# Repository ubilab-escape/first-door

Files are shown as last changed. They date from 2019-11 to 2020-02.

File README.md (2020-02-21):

# Group 4:  First door #
Our group works on the automated doors in the escape room as well on the puzzle for the first door.

## Content
* [Part in the Escape Room](#1)
* [Project Timeline](#2)
* [Using the code](#7)
* [First Puzzle](#4)
* [Doors](#5)
* [Plasma Globes](#6)

## Part in the Escape Room 
After the mission briefing the participants will enter the anterior room.
In the story this will be the room of the security even though the security will be absent for the whole game.

The participants have to solve a first puzzle to open the first door and to be able to move to the second, adjencted room which will be the computer lab room. After all players are situated in the second room, the first door should close.

There the players again have to solve various riddles and puzzle to get into the server room. The door between lab and serverroom will be implemented by us.

## Project Timeline 
- [x] Concept finding for door mechanism, puzzles and dead man switches
- [x] Composition of a part list
- [x] Installing of the doors
- [x] Software development of the doors and electrical installation
- [x] Software development of the riddle and installation of its needed components
- [x] Software development of the MQTT communication
- [x] Testing of the door and riddle components over MQTT
- [x] Testing of the voltage/current course of the plasma globes
- [x] Software implementation of the plasma globes
- [x] 3D printing of fixations and riddle housing
- [x] Testing of the interaction of all components
- [x] Implementation and control over the LED stripes from the Environment Group
- [x] Last testing and bug fixing
- [x] Final run and presentation

## Using the Code 
### General
* WiFi- credentials are not included in the code. Before uploading via OTA, ensure that the correct WiFi credentials are set in the code!

### Door Code
* Ensure that the #define macro DOOR1 or DOOR2 is set according to which door you want to use the code for

### Plasma Globes
* When you change the mdns name via MQTT, this will also change the ID of the globe (gets written to EEPROM). Use the Format "GlobeX" as new name, e.g. "Globe0" for the Master Globe.
* Max. 4 globes can be used (IDs: 0,1,2,3)

### MQTT interaction
* The commands for controlling the implemented stages can be found in the document linked at the end of this readme!

## First Puzzle 
### Stage ###
After the mission briefing, the participants are in the anteroom and need to get access to the labroom.

### Concept and Idea ###
Story: The absent security man likes to listen to music on his MP3-Player while at work. This MP3 contains several songs as well as an **audio morse code**. Using the help of a hidden morse alphabet in the room the players will be able to solve the puzzle and obtain a code.
Morse alphabet test

The obtained code has to be inserted into a keypad with an LCD display.

### Hardware ###
* MP3 Player
* 3D printed Input interface consisting of 
	* LCD display
	* 4x4 matrix keypad
	* ESP32

The parts for 3D printing the input interface can be founded [here](https://github.com/ubilab-escape/first-door/tree/master/3D%20Printing)
### Software ###
[Code](https://github.com/ubilab-escape/first-door/tree/master/Final%20Code/First_Puzzle_final)

The following flow chart only represents the basic function of the code and does not show every detail!

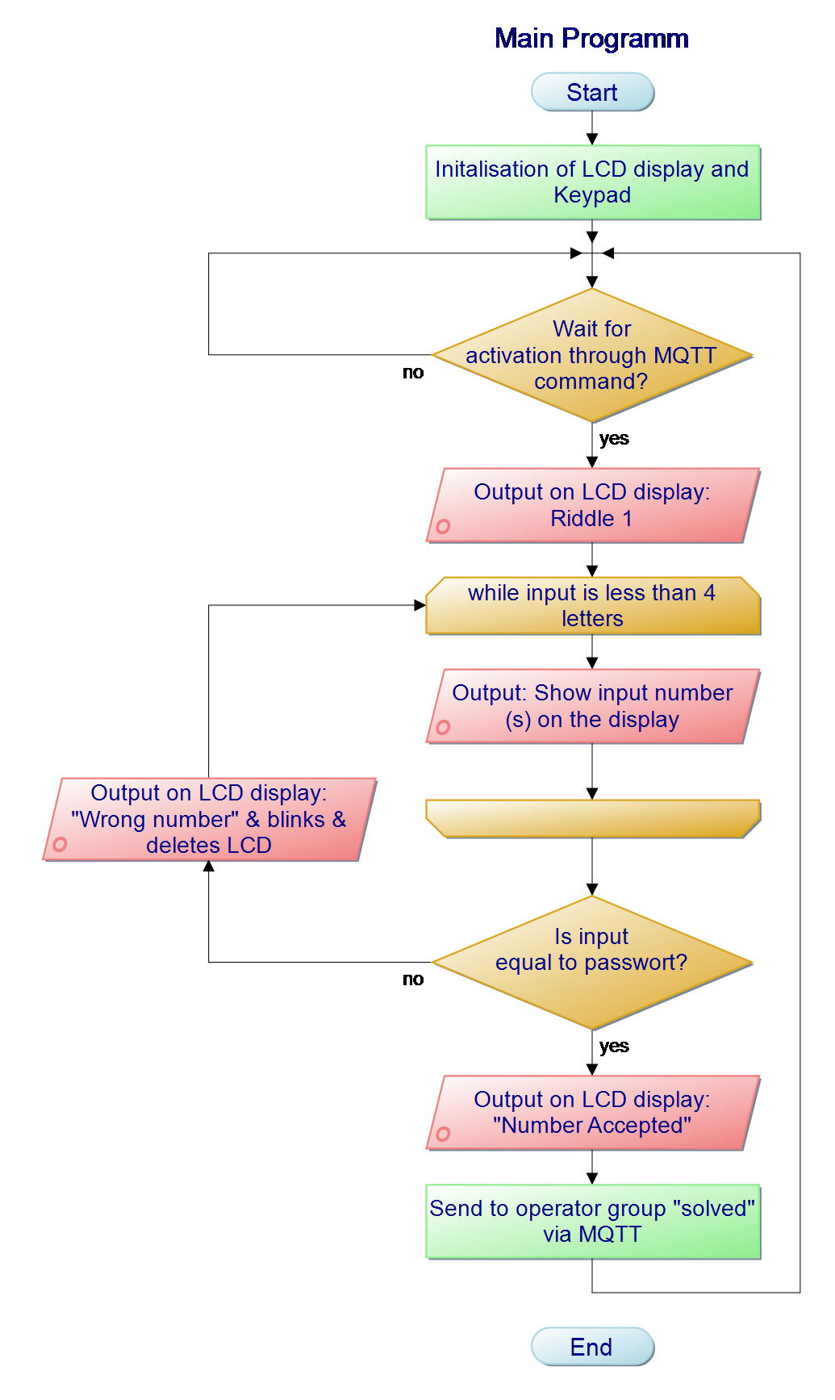
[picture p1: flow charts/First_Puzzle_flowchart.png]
flow chart puzzle 1


## Doors 
### Stage ###
Door 1:
This is the door between anteroom and labroom. This door should open after solving the first puzzle (Morse Code Puzzle) and close after all participants entered the labroom. After the participants were able to solve all other riddles the door should open again to let the players escape.

Door 2:
This door seperates the labroom from the serverroom. After solving all puzzles in the labroom this door will open automatically and provide access to the serverroom.

### Concept and Idea ###
* both doors should open automatically and have to be controllable by the operator via MQTT commands
* a detection mechanism should be implemented for localization of participants standing in between the door frame while closing
* the participants shouldn't be able to open the doors manually by hand (--> lock)

A concept of a sliding door with a toothbelt mechanism was developed. The door is suspended and guided through a linear sliding rail on the upper door frame. Furthermore a U-profile duct was mounted for guidance at the bottom. The door movement is achieved by a toothbelt mechanism. Both ends of the toothbelt are fixed on the door. Return shafts on both sides of the door frame are redirecting the toothbelt. Also one return shaft is connected to the stepper motor axes. Mechanical switches (endstops) on both sides detect either closed or opened position.

An obstacle detection in the closing area could be avoided through the usage of the Plasma Globes. Every participant in the Escape Room has to touch one Plasma Globe for closing the door. A person in the closing area is therefore impossible. Also, the toothbelt slides over the return shaft, as soon as the door faces a slight resistance.

Not implemented / possible improvements:
* electrical door lock: solved by leaving driving stage "on" while door is closed, so that more force is needed to push it open.

### Hardware ###
* ESP32
* stepper motor + appropriate driver
* 24V power supply
* buck converter for ESP32 power supply (24V --> 5V)
* tooth belt
* toothbelt disk
* end stop switches
* linear rail
* sliding suspension bracket
* door material (wooden plates)
* U-profile duct

### Software
[Door - Code](https://github.com/ubilab-escape/first-door/tree/master/Final%20Code/Door)

In the following the velocity profile of the door is shown. 

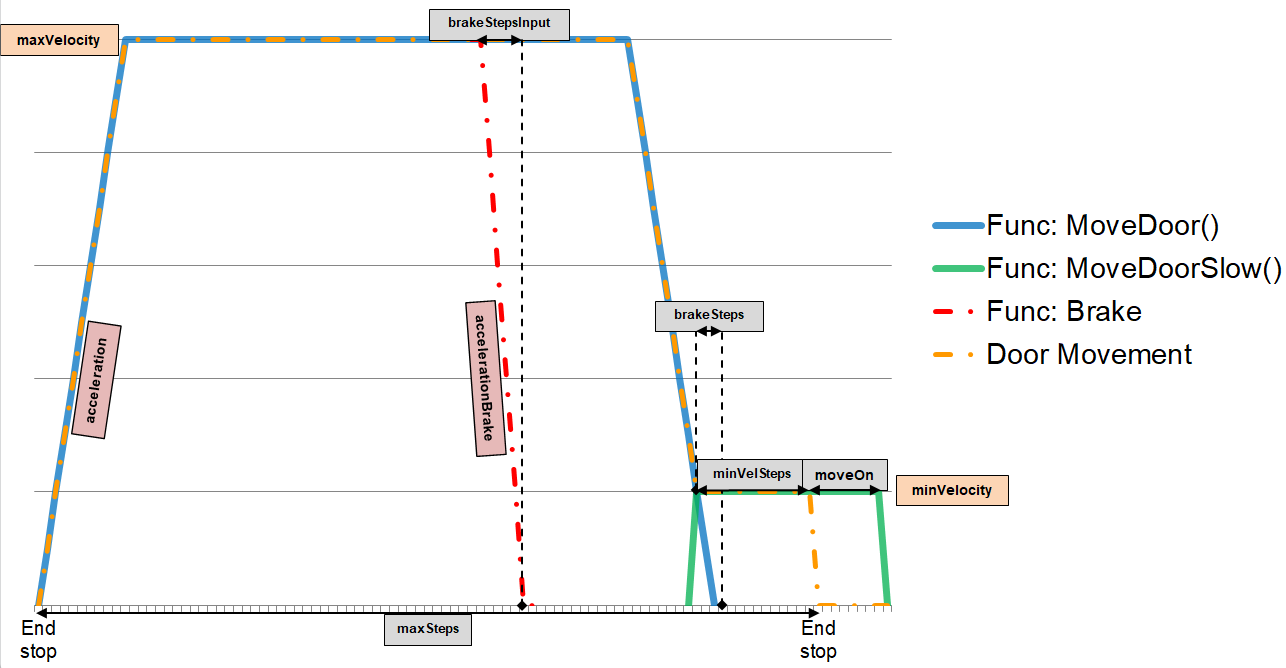
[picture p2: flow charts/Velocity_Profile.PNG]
Velocity_profile


* Acceleration, velocity and distance parameters (acceleration / accelerationBrake / maxVelocity / minVelocity / minVelSteps / moveOn) must be chosen before code flashing.
* The parameters brakeSteps and brakeStepsInput are calculated by 0.5*minvelocity^2/acceleration or 0.5*maxVelocitty^2/accelerationBrake. 
* The parameter maxSteps is set and the variable curPos is reset after calibration.

The programming flowchart is attached in the following. The flow chart only represents the basic function of the code and does not show every detail!

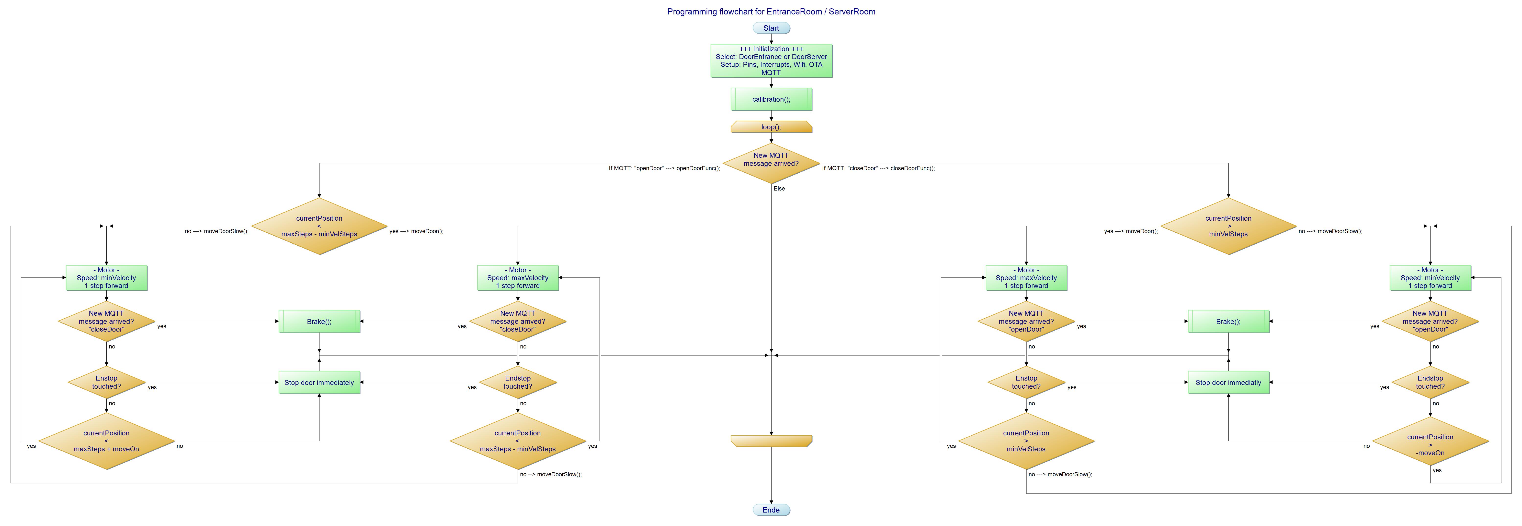
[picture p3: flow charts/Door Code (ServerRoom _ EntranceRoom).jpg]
FlowChart_door


## Plasma globes 
### Stage ###
When the first door opens, participants enter the labroom. There, all lights are off and the plasma globes are activated. The participants must touch all plasma balls simultaneously so that the first door can close and the game continues.

### Concept and Idea ###
* plasma globes draw significantly more current when touched so they can be used as switch
* 4 plasma globes spread across the room at the walls (not possible to touch more than one globe simultaneously)
* Each plasma globe is a standalone unit with own "PowerMeter"
* One "master" device, the other globes are slaves
* operator sends #participants, then each globe determines if it is activated or deactivated (according to globe ID which can be set over MQTT)
* Slave globes:
	* check if globe is touched
	* send touched/ untouched message to master globe
* Master globes:
	* check if globe is touched
	* count number of touched slaves
	* trigger opening of door if all participating globes are touched simultaneously
	* trigger closing of door if not all participating globes are touched
	* activate environment LEDs according to number of touched slaves to provide feedback to the user
	* deactivates all globes as soon as door is closed and send puzzle solved message

### Hardware ###
* PowerMeter (hardware box containing ESP8266 and AC current/voltage sensor )
* 4 usb powered plasma globes

The files for the 3D printed mounting can be found [here](https://github.com/ubilab-escape/first-door/tree/master/3D%20Printing)

### Software ###
[Master Globe - Code](https://github.com/ubilab-escape/first-door/tree/master/Final%20Code/PowerMeter_plasma_master)

[Slave Globe - Code](https://github.com/ubilab-escape/first-door/tree/master/Final%20Code/PowerMeter_plasma_slaves)

The following flow chart only represents the basic function of the code and does not show every detail!
This flow chart represents the master instance, slaves work similar, but without logic for door interaction.
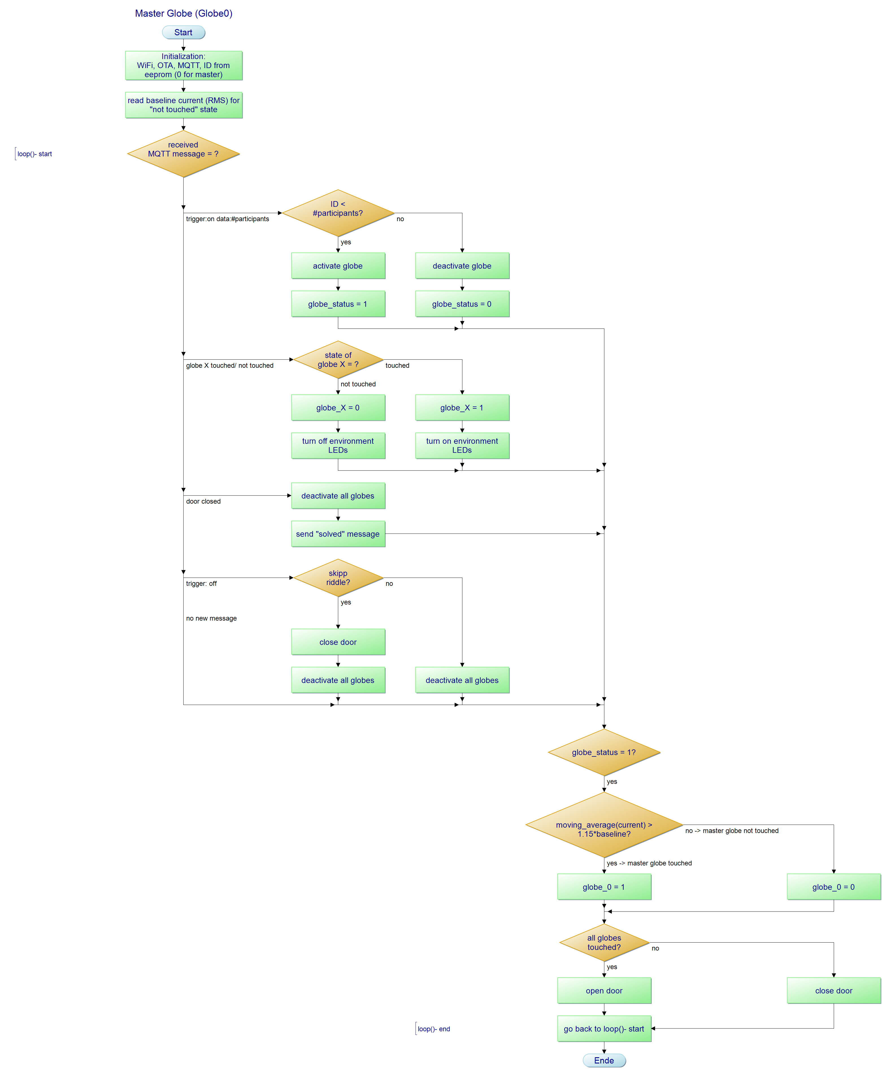
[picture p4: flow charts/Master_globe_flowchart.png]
flow chart puzzle 1


## MQTT Communication ##
The MQTT communication that was initially developed with the operator group can be found here (not every detail was implemented):
* [Doors](https://github.com/ubilab-escape/operator/blob/master/doc/design/group_4_door.svg "Doors")
* [First Puzzle](https://github.com/ubilab-escape/operator/blob/master/doc/design/group_4_puzzle_entrance_door.svg "First Puzzle")
* [Plasma Globe Puzzle](https://github.com/ubilab-escape/operator/blob/master/doc/design/group_4_puzzle_globes.svg "Plasma Globe Puzzle")

For controlling the described escape room parts of our group, use the commands in the following document:
[MQTT commands](https://github.com/ubilab-escape/first-door/blob/master/MQTT_publish_messages.docx "MQTT commands")

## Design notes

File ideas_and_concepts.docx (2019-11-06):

Ideas of Group #4: Both doors & first puzzle

Puzzle:

A wooden cylinder is physically given with a cord which is wound exactly four times around the cylinder. Thereby one end of the cord must touch one end of the cylinder so that the cord extends over the entire cylinder (see figure).

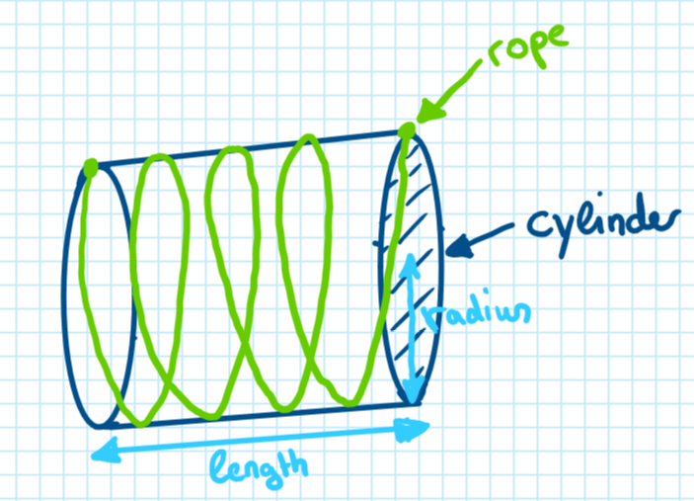
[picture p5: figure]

The task is to calculate the length of the cord. Given parameters are the radius and the length of the cylinder.

The result must then be entered into a keypad (binary or decimal system). If the result is correct the first door will open and the participants will get access for the lab room.

Doors:

- Doors

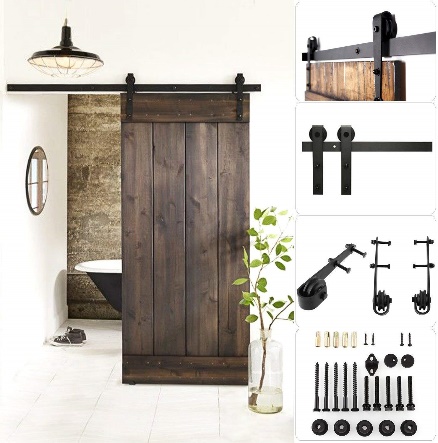
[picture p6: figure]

- Material: Wooden door, either old door which we cut in size or wood board
- Mounting: Sliding door mounting e.g.
- Other required hardware:
  - Screws and nails
  - Percussion drill
  - Drill machine
- Mechanism
  - Alternative A: Pull rope mechanics

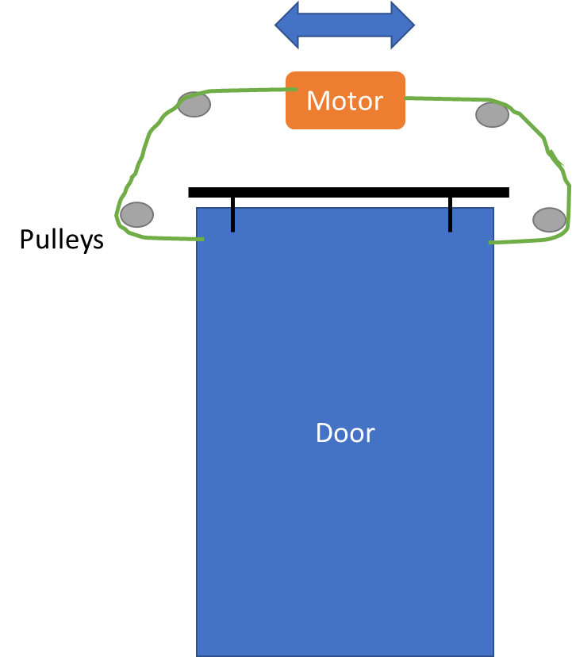
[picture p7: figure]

Required hardware: Pulleys, gearwheels, rope, mounting devices

  - Alternative B: Gear mechanics

3) Detection of objects in closing area

Concept: Use infrared emitter and sensors to detect if the door area is free in order to close the door.

Also use a pressure sensor to feedback that the door is closed

4) Detection of participants in Lab Room:

- Concept A: Dead-man-switches spread across lab room have to be activated → 1st door closes and adventure continues
- Hardware: Plasma globe / simple switch, current sensor (shunt resistor), uC/ relais, wiring
- Current flow through plasma globe changes when touched by hands → measure current flow with shunt resistor and close door when each plasma globe is touched (make sure by positioning that no person can reach more than one plasma globe simultaneously)
- Remark: Reliability of “plasma globe switch” has to be tested and in worst case exchanged by simple button switches
- Concept B: Using Group 9 locating the group members

Other required hardware

- Microcontroller with WLAN function / shield

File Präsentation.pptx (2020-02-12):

## Project „Escape Room“

Group 4 – Doors and first puzzle
David, Mario, Sarah

## Interactions

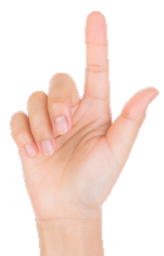
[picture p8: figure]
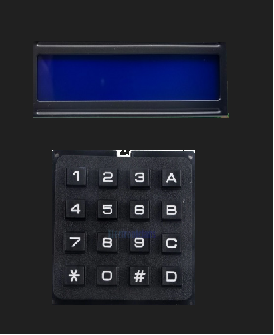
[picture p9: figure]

RIGHT

open

## Interactions

close

## How does this communciation work? -> MQTT

Puzzle

Activated/inactivated

open/close

Door 1

solved

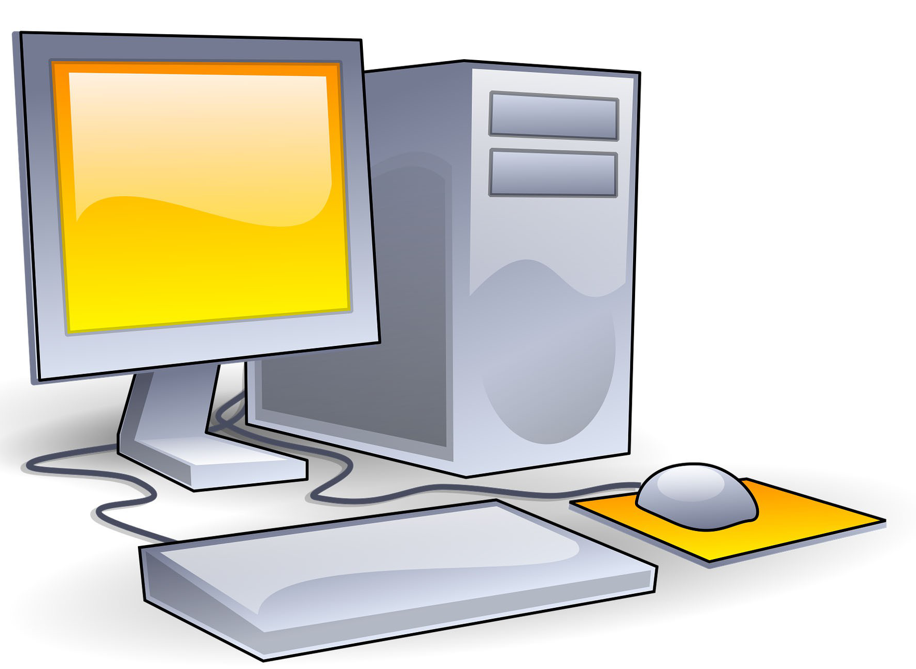
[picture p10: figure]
Bildergebnis für computer

Server

open/close

Door 2

open/close

Activated/
inactivated

Touched/
not touched

Globes

## Puzzle

Components:
- 16x2 IC2 LCD Display
- 4x4 Matrix Keypad
- 3D printed housing
Microcontroller:
- ESP32
Communication between microcontroller and components:
- I2C Interface to LCD display
- Analog Inputs to Keypad

## Puzzle

no

Right password entered?

Initialisation

yes

Send via MQTT: Puzzle solved -> Door will open

## Doors

Mechanical components:
- Mounting
- Gearbelts
- Gearwheels
- Floor guide rail
- Endstops
Electrical compnents:
- Motor and Driver
- Endstops switches
- Voltage supply
Microcontroller:
- ESP 32

## Doors

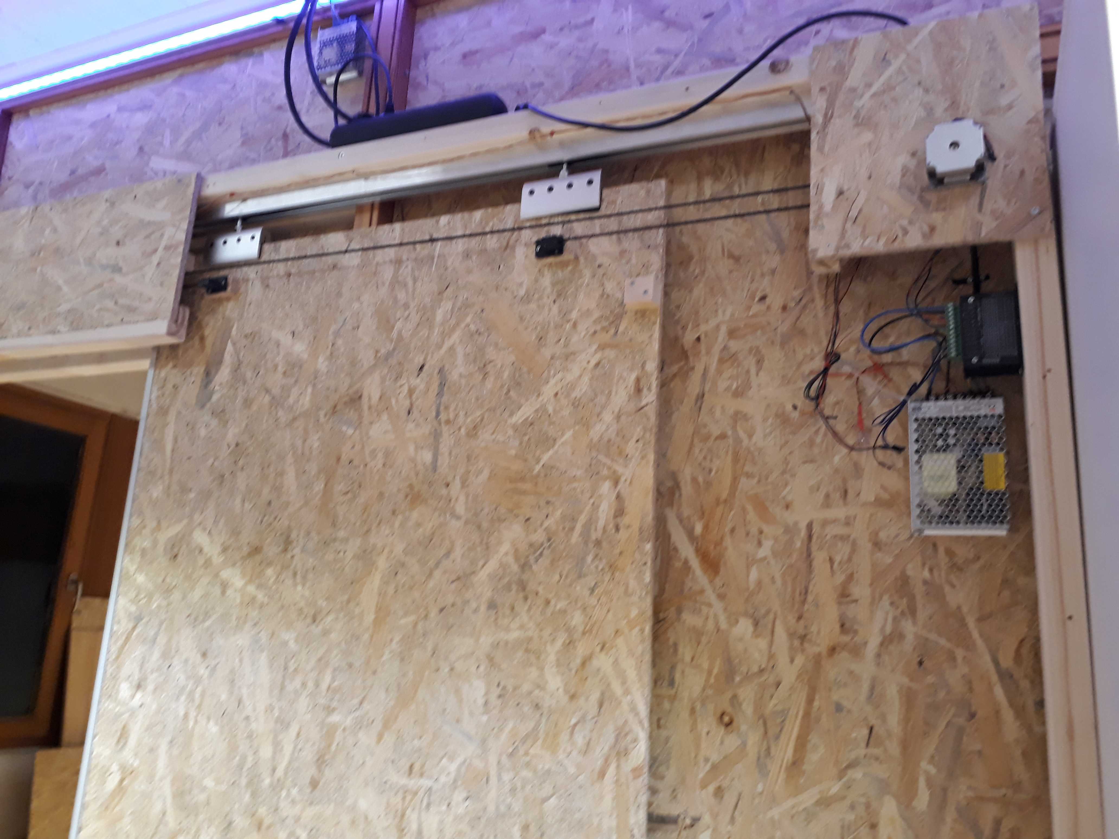
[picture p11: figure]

Mechanical components:
- Mounting
- Gearbelts
- Gearwheels
- Floor guide rail
- Endstops
Electrical compnents:
- Motor and Driver
- Endstops switches
- Voltage supply
Microcontroller:
- ESP 32

## Doors – Functional principle

Initialisation

Slowly move door in one direction

Endstop
touched?

yes

Repeat some for other side

Save Endpositions

no

Move the door to the respective end stop

Move the door to the respective end stop

Get command: „open“

Send MQTT message: open

Send MQTT message: closed

Get command: „close“

## Plasma Globes – Sensing touch events

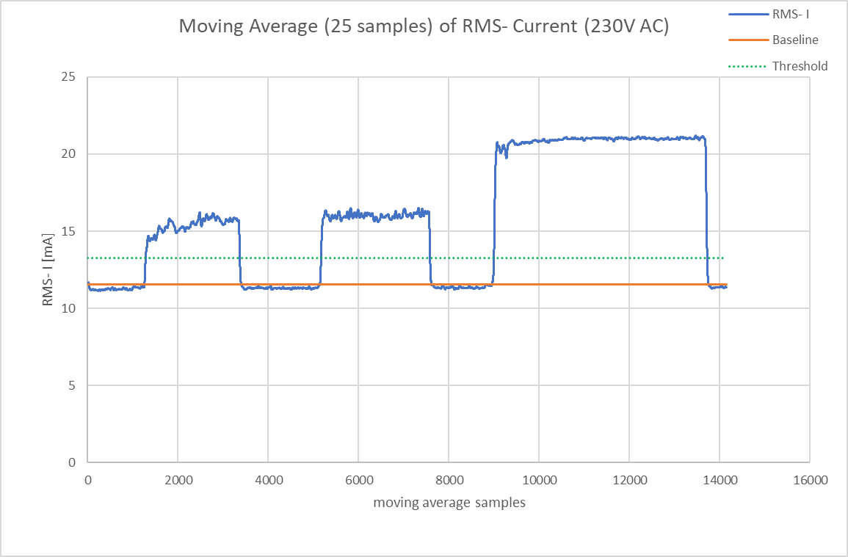
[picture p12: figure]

touched

touched

touched

## Plasma Globes - Puzzle

open/close

touched/ not touched

closed!

close

open

master

touched/ not touched

slave

touched/ not touched

slave

slave

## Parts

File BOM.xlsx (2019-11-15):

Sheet: Finale_BOM
BOM | Teil | Eigenschaften | Kosten | Stück |  | Link
Tür
Mechanik oben: Set |  |  | 34.65 | 2 | 69.3 | https://www.amazon.de/GEZE-Rollan-Schiebet%C3%BCrbeschlag-Schiebet%C3%BCr-T%C3%BCrbreite/dp/B000VD8YI6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
Führungsschiene unten |  | U- Profil |  |  | 0 | Baumarkt
Rahmen |  |  |  |  | 0
Konstruktionsvollholz |  |  | 35 € | 1 | 35 | https://www.obi.de/bauholz/konstruktionsvollholz-brettschichtholz/c/1823
Schrauben |  |  |  |  | 0
Tür |  |  |  |  | 0
Sperrholz Pappel |  |  | 18 € | 2 | 36 | https://www.bauhaus.info/zuschnittplatten/sperrholzplatte-nach-mass/p/24815310
 |  |  |  |  | 0
Antrieb |  |  |  |  | 0
Zahnriemen GT2 (M) 10mm |  |  | 9 |  | 0 | https://www.amazon.de/ASHATA-Zahnriemen-3D-Drucker-Riemenscheibe-Synchronriemen-3-Meter/dp/B07PFD7H78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
Zahnriehmenklemmen |  |  |  |  | 0 | Amazon
Zahnriehmenscheiben |  |  |  |  | 0 | Amazon
 |  |  |  |  | 0
Türsicherheit |  |  |  |  | 0
Lichtquelle |  |  | 5 | 1 | 5 | https://www.amazon.de/AZDelivery-%E2%AD%90%E2%AD%90%E2%AD%90%E2%AD%90%E2%AD%90-KY-008-Sensor-Arduino/dp/B07CNGFS8M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
Lichtsensor |  |  | 6 | 1 | 6 | https://www.amazon.de/AZDelivery-Widerstand-Photoresistor-LDR5528-Arduino/dp/B07DDN5TH2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
 |  |  |  |  | 0
Türschloss |  |  |  |  | 0
elektromagn. Riegel |  |  | 16 | 1 | 16 | https://www.amazon.de/ATOPLEE-T%C3%BCr-Fach-Zunge-Down-Elektroschloss-Montag-Magnet-554239mm/dp/B01N650528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
elektromagn. Riegel |  |  | 9 | 2 | 18 | https://www.amazon.de/BQLZR-Schrankt%C2%A8%C2%B9r-Elektroschloss-Montage-Solenoid/dp/B00NE0GHDW
Relais |  |  | 6.19 | 1 | 6.19 | https://www.amazon.de/AZDelivery-1-Relais-KY-019-High-Level-Trigger-Arduino/dp/B07CNR7K9B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
Keypad |  |  | 6 | 1 | 6 | https://www.amazon.de/AZDelivery-4x4-Matrix-Keypad-Tastatur/dp/B07D2FGQL4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
Display |  |  | 5 | 1 | 5 | https://www.amazon.de/dp/B07CQG6CMT
Buck Converter | DC/DC- Wandler | 24V(Netzteil) --> 12V (Riegel) | 3 | 1 | 3 | https://www.conrad.de/de/p/mini-dc-dc-step-down-spannungsregler-mp1584en-buck-power-module-outout-0-8-20v-3a-802244075.html
 |  |  |  |  | 0
Motor- Antrieb |  |  |  |  | 0
Netzteil |  |  |  |  | 0
 | MW LRS-150F-24 Schaltnetzteil | 150 W, 24 V, 6,5 A | 21.65 | 1 | 21.65 | https://www.reichelt.de/schaltnetzteil-geschlossen-150-w-24-v-6-5-a-mw-lrs-150f-24-p202982.html?trstct=pos_6
Kaltgerätestecker |  |  |  |  | 0
 |  |  |  |  | 0
Stromsensorik |  |  |  |  | 0
Motor | INA219- Modul, Billig- Version | Strom- und Spannungsmessung (0,8mA Auflösung) | 2.8 | 5 | 14 | https://www.reichelt.de/entwicklerboards-stromsensor-mit-breakoutboard-ina219-debo-sens-power-p266047.html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
 | Eigenlösung? |  |  |  | 0
Plasmakugel | INA219-Modul (s.o.) |  |  | 1 | 0
 | Eigenlösung? |  |  |  | 0
 |  |  |  |  | 0
Dead-man-switch |  |  |  |  | 0
Plasmakugel | PEARL Plasmalampe | USB, 9cm | 9.95 | 4 | 39.8 | https://www.amazon.de/PEARL-Plasmalampe-USB-Plasmakugel-Arbeitsplatz-Plasma/dp/B004DAHH3Q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
 |  |  |  |  | 0
Sonstiges |  |  |  |  | 0
Buck-Converter ESP32 | DC/DC Converter | 24V(Netzteil) --> 5V (ESP32) | 3.45 | 2 | 6.9 | https://www.conrad.de/de/p/dc-dc-9v-12v-24v-to-5v-3a-step-down-voltage-regulator-power-modul-car-charger-802244039.html
Summe |  |  |  |  | 287.84

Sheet: Tabelle1
BOM | Teil | Eigenschaften | Kosten | Stück | Link
Tür
Mechanik oben: Set |  |  | 34.65 | 2 | https://www.amazon.de/GEZE-Rollan-Schiebet%C3%BCrbeschlag-Schiebet%C3%BCr-T%C3%BCrbreite/dp/B000VD8YI6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
Führungsschiene unten |  | U- Profil |  |  | Baumarkt
Rahmen
Konstruktionsvollholz |  |  | 35 € | 1 | https://www.obi.de/bauholz/konstruktionsvollholz-brettschichtholz/c/1823
Schrauben
Tür
Sperrholz Pappel |  |  | 18 € | 2 | https://www.bauhaus.info/zuschnittplatten/sperrholzplatte-nach-mass/p/24815310
Antrieb
Zahnriemen GT2 (M) 10mm |  |  | 9 |  | https://www.amazon.de/ASHATA-Zahnriemen-3D-Drucker-Riemenscheibe-Synchronriemen-3-Meter/dp/B07PFD7H78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
Zahnriehmenklemmen |  |  |  |  | Amazon
Zahnriehmenscheiben |  |  |  |  | Amazon
Türsicherheit
Lichtquelle |  |  | 5 | 1 | https://www.amazon.de/AZDelivery-%E2%AD%90%E2%AD%90%E2%AD%90%E2%AD%90%E2%AD%90-KY-008-Sensor-Arduino/dp/B07CNGFS8M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
Lichtsensor |  |  | 6 | 1 | https://www.amazon.de/AZDelivery-Widerstand-Photoresistor-LDR5528-Arduino/dp/B07DDN5TH2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
Türschloss
elektromagn. Riegel |  |  | 16 | 1 | https://www.amazon.de/ATOPLEE-T%C3%BCr-Fach-Zunge-Down-Elektroschloss-Montag-Magnet-554239mm/dp/B01N650528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
elektromagn. Riegel |  |  | 9 | 2 | https://www.amazon.de/BQLZR-Schrankt%C2%A8%C2%B9r-Elektroschloss-Montage-Solenoid/dp/B00NE0GHDW
Relais |  |  | 6.19 | 1 | https://www.amazon.de/AZDelivery-1-Relais-KY-019-High-Level-Trigger-Arduino/dp/B07CNR7K9B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
Motor- Antrieb
Netzteil
24V | MW LRS-150F-24 Schaltnetzteil | 150 W, 24 V, 6,5 A | 23.2 | 1 | https://www.reichelt.de/schaltnetzteil-geschlossen-150-w-24-v-6-5-a-mw-lrs-150f-24-p202982.html?trstct=pos_6
 | MW RSP-200-24 | 200 W, 24 V, 8,4 A | 43.65 |  | https://www.reichelt.de/schaltnetzteil-geschlossen-200-w-24-v-8-4-a-mw-rsp-200-24-p147909.html?trstct=pos_0
12V | Basetech PSDD-60-12 | 12 V 5 A 60 W | 23.99 |  | https://www.conrad.de/de/p/basetech-psdd-60-12-hutschienen-netzteil-din-rail-12-v-5-a-60-w-2-x-1698265.html
 | MW LRS-150F-12 Schaltnetzteil | 150 W, 12 V, 12,5 A | 24.5 |  | https://www.reichelt.de/schaltnetzteil-geschlossen-150-w-12-v-12-5-a-mw-lrs-150-12-p202985.html?trstct=pos_8
Kaltgerätestecker
Stromsensorik
Motor | INA219- Modul, Billig- Version | Strom- und Spannungsmessung (0,8mA Auflösung) | 2.8 | 1 | https://www.reichelt.de/entwicklerboards-stromsensor-mit-breakoutboard-ina219-debo-sens-power-p266047.html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
 | INA219- Modul, Adafruit | Strom- und Spannungsmessung (0,8mA Auflösung) | 10.4 |  | https://www.reichelt.de/entwicklerboards-dc-stromschalter-debo-sens-dc-p235508.html?PROVID=2788&r=1
 | Eigenlösung?
Plasmakugel | INA219-Modul (s.o.) |  |  | 1
 | Eigenlösung?
Dead-man-switch
Plasmakugel | PEARL Plasmalampe | USB, 9cm | 9.95 | 1(4) | https://www.amazon.de/PEARL-Plasmalampe-USB-Plasmakugel-Arbeitsplatz-Plasma/dp/B004DAHH3Q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

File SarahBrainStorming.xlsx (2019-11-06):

Topic | Object | Varianten | Materials | Size/ Technical Data | Comments
Hardware | Doors |  | Wood /Door | 10-20cm größer als Tür | Holz in den Raum bevor zuschneiden, da shrinking occurs
 |  |  |  |  | https://toom.de/p/profiltuer-kiefer-474-x-394-mm/7301811
 | Aufhängungssystem |  | Eisen | An Tür angepasst | https://www.amazon.de/Schiebet%C3%BCrbeschlag-Laufschienen-H%C3%A4ngeschiene-Schiebet%C3%BCrsystem-Schiebet%C3%BCren/dp/B07DLTNC8Y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
 | Bodenführung? |  | Eisen | An Tür angepasst
Automatic | Mechanics | "Rope Pull Mechanics" | Rope (Nylon, Climbing gear) |  | For explanation see next page
 |  |  | Power motor
 |  |  | Springs
 |  |  | deflection pulleys
 |  |  | mounting devices
 |  | Zahnradmechanik
 |  |  | Stepper Motor
 |  |  | Gearwheels
 |  |  | gear belt
 |  |  | Mounting devices
 | Sensors | Contactless Sensors | Infrared Sensors
 |  | Contact Sensors | Pressure Sensors
Miscancellous | Microcontroller
 | Wiring
 | Power for Motor

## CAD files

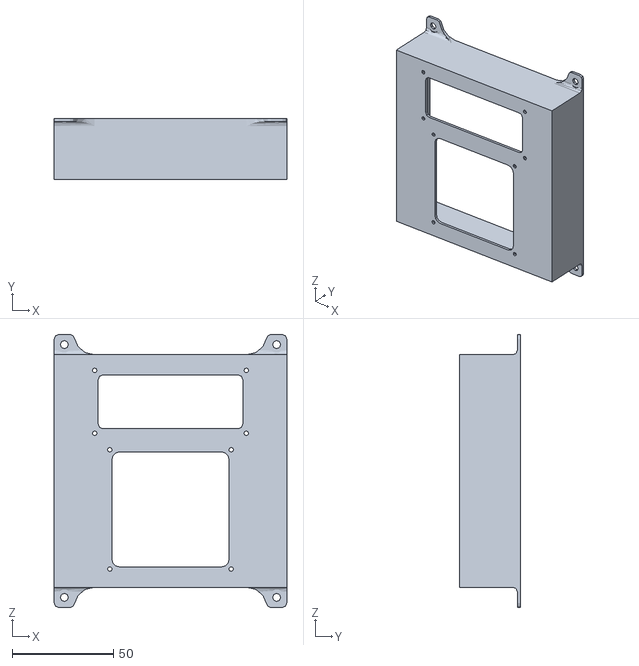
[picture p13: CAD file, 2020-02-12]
3D Printing/deckel_s_1_5_aussparung.stl
115.0 x 30.0 x 135.0

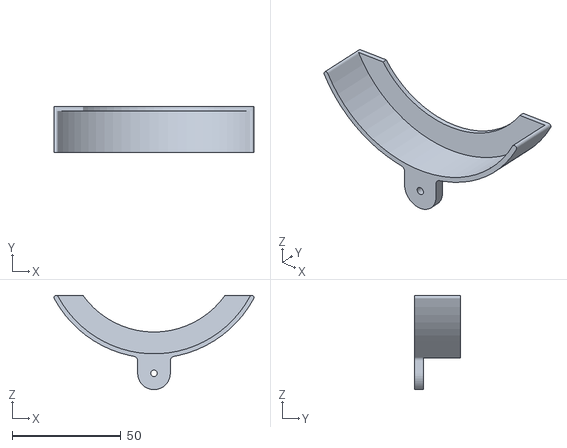
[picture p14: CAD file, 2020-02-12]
3D Printing/HalterungGlobesStandard_Unten.STL
91.8 x 21.0 x 43.2

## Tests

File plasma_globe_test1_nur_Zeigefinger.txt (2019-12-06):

2357.90
2359.80
2358.12
2354.07
2358.39
2358.22
2353.92
2359.21
2353.96
2356.58
2357.98
2354.14
2358.77
2355.48
2354.96
2357.62
2354.01
2354.20
2359.39
2361.41
2356.26
2360.90
2357.60
2354.65
2356.68
2359.03
2357.72
2355.50
2357.16
2357.20
2357.32
2355.88
2360.36
2353.42
2359.20
2360.44
2350.24
2355.43
2355.61
2356.55
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

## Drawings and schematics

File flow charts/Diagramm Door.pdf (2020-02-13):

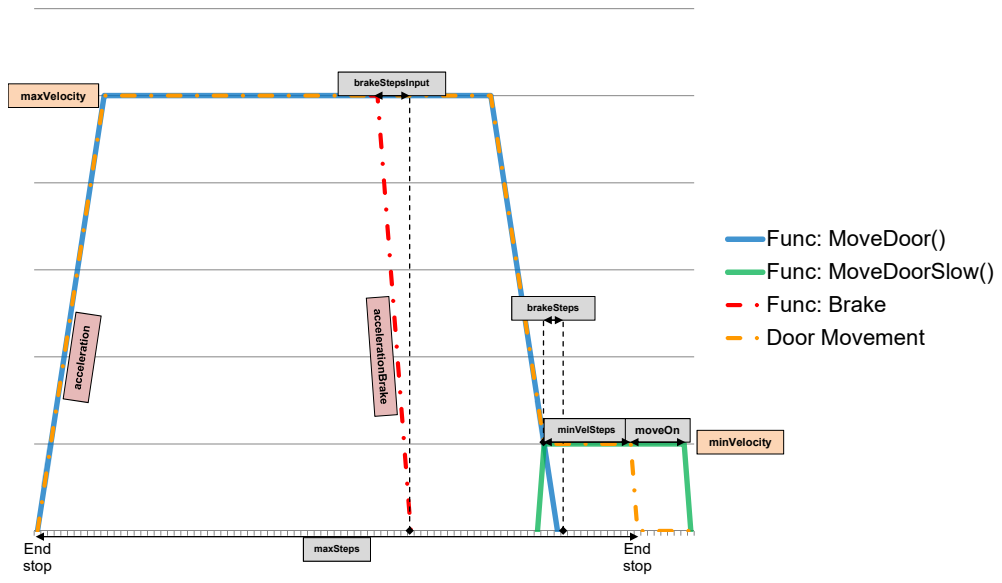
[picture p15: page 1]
End stop; Func: MoveDoor() Func: MoveDoorSlow() Func: Brake Door Movement; maxVelocity; minVelocity; brakeStepsInput; brakeSteps; minVelSteps; moveOn; maxSteps

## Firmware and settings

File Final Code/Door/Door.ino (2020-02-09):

//--------------Ubilab - Escape Room WS 2019---------------------
//-----------Group 4 - Both doors + Entry Puzzle-----------------
//Code for motor control of the sliding door (Labroom --> Server room)


//++++++++++++++++++++++++++++++++++++++++++++++++++++++++++++++++++++++++++++++++++++++++++++++++++++++++++++++++++++++++++++++++++++++++++++++++++++++
//+++++++++++++++++++++++++++++++++++++++++++++++++++++++++++++ Libraries ++++++++++++++++++++++++++++++++++++++++++++++++++++++++++++++++++++++++++++++++
//++++++++++++++++++++++++++++++++++++++++++++++++++++++++++++++++++++++++++++++++++++++++++++++++++++++++++++++++++++++++++++++++++++++++++++++++++++++

#include "WiFi_MQTT_Json_Motor.h"
#include <WiFi.h>
#include <PubSubClient.h>
#include <ArduinoJson.h>
#include <ESPmDNS.h>
#include <WiFiUdp.h>
#include <ArduinoOTA.h>
#include <EEPROM.h>
#include <AccelStepper.h>

//For code debugging
//#define DEBUG

//**********************************IMPORTANT*********************************************************************************************************
//This should be either "DOOR1" or "DOOR2" for the respective door
#define DOOR1

//++++++++++++++++++++++++++++++++++++++++++++++++++++++++++++++++++++++++++++++++++++++++++++++++++++++++++++++++++++++++++++++++++++++++++++++++++++++
//+++++++++++++++++++++++++++++++++++++++++++++++++++++++++++++ Variables ++++++++++++++++++++++++++++++++++++++++++++++++++++++++++++++++++++++++++++++++
//++++++++++++++++++++++++++++++++++++++++++++++++++++++++++++++++++++++++++++++++++++++++++++++++++++++++++++++++++++++++++++++++++++++++++++++++++++++
//wifi, mqtt clients
WiFiClient wifiClient;
PubSubClient client(wifiClient);

//ESP 32 Pin Connections

//...for Door1
#ifdef DOOR1
#define enPin 25
#define dirPin 32
#define pulPin 33
#define interruptOpenPin 26
#define interruptClosePin 23
#endif

//...for Door2
#ifdef DOOR2
#define enPin 25
#define dirPin 32
#define pulPin 33
#define interruptOpenPin 18
#define interruptClosePin 27
#endif

AccelStepper door1(1, pulPin, dirPin); // Pin assignment for the library

//Moving parameters
const int acceleration = 1300;
const int accelerationBreak = 1500;
const int maxVelocity = 3000;
const int minVelocity = 300; //unter 300 steps/sec -->microstepping : Dann alle Steps mit Faktor multiplizieren
const int calVelocity = 700;
const int minVelSteps = 500;   //300
const int breakSteps = 0.5 * sq(minVelocity) / acceleration ;
const int moveOn = 300;
float actSpeed;
const int breakStepsInput = 0.5 * sq(maxVelocity) / accelerationBreak;

//Moving variables
int curPos;
int endPosition;
int maxSteps;

bool brakeOpen = false;
bool brakeClose = false;



//Interrupt variables
volatile int interruptFlagO = 0;
volatile int interruptFlagC = 0;

//variables for alarm light
#ifdef DOOR1
String light_topic = "powermeter/gyrophare1/switch";
#endif
#ifdef DOOR2
String light_topic = "powermeter/gyrophare2/switch";
#endif


//++++++++++++++++++++++++++++++++++++++++++++++++++++++++++++++++++++++++++++++++++++++++++++++++++++++++++++++++++++++++++++++++++++++++++++++++++++++
//+++++++++++++++++++++++++++++++++++++++++++++++++++++++++++++ SETUP ++++++++++++++++++++++++++++++++++++++++++++++++++++++++++++++++++++++++++++++++
//++++++++++++++++++++++++++++++++++++++++++++++++++++++++++++++++++++++++++++++++++++++++++++++++++++++++++++++++++++++++++++++++++++++++++++++++++++++
void setup() {

  Serial.begin(115200);

  //Pin declaration
  pinMode(enPin, OUTPUT);
  pinMode(dirPin, OUTPUT);
  pinMode(pulPin, OUTPUT);
  pinMode(interruptOpenPin, INPUT_PULLUP);
  pinMode(interruptClosePin, INPUT_PULLUP);

#ifdef DOOR1
  pinMode(14, OUTPUT);
  digitalWrite(14, HIGH); //Supply for LED on endstop board
  pinMode(27, OUTPUT);
  digitalWrite(27, LOW); //GND for endstop board
#endif

#ifdef DOOR2
  pinMode(21, OUTPUT);
  digitalWrite(21, HIGH); //Supply for LED on endstop board
  pinMode(19, OUTPUT);
  digitalWrite(19, LOW); //GND for endstop board
#endif

  //Interrupt for door stop detection
  attachInterrupt(digitalPinToInterrupt(interruptOpenPin), interruptOpen, FALLING); //Interrupt at the end of door opening due to switch touching
  attachInterrupt(digitalPinToInterrupt(interruptClosePin), interruptClose, RISING); //Interrupt at the end of door closing due to switch touching

  setup_wifi();
  setupOTA();
  setup_mqtt();
  //start MQTT communication
  mqtt_loop();

  //after wifi stuff calibrate the door!
  //turn alarm light on
  client.publish(light_topic.c_str(), "on");
  calibration();

  //after calibration open the door that all rooms are open
  openDoor = true;
  openDoorFunc();
  openDoor = false;

  //turn alarm light off
  client.publish(light_topic.c_str(), "off");
}


//++++++++++++++++++++++++++++++++++++++++++++++++++++++++++++++++++++++++++++++++++++++++++++++++++++++++++++++++++++++++++++++++++++++++++++++++++++++
//+++++++++++++++++++++++++++++++++++++++++++++++++++++++++++++ LOOP ++++++++++++++++++++++++++++++++++++++++++++++++++++++++++++++++++++++++++++++++
//++++++++++++++++++++++++++++++++++++++++++++++++++++++++++++++++++++++++++++++++++++++++++++++++++++++++++++++++++++++++++++++++++++++++++++++++++++++
void loop() {
  //reconnect to Wifi
  if (WiFi.status() != WL_CONNECTED) {
    setup_wifi();
  }

  // Arduino OTA
  ArduinoOTA.handle();

  //(re-) connect to mqtt server and check for incoming messages
  mqtt_loop();

  if (openDoor == true) {
    
    //activate alarm light
    client.publish(light_topic.c_str(), "on");
    openDoorFunc();
    openDoor = false;
    //turn alarm light off
    client.publish(light_topic.c_str(), "off");
    
  }
  else if (closeDoor == true) {
    //activate alarm light
    client.publish(light_topic.c_str(), "on");
    closeDoorFunc();
    closeDoor = false;
    //turn alarm light off
    client.publish(light_topic.c_str(), "off");
  }

}
//++++++++++++++++++++++++++++++++++++++++++++++++++++++++++++++++++++++++++++++++++++++++++++++++++++++++++++++++++++++++++++++++++++++++++++++++++++++
//+++++++++++++++++++++++++++++++++++++++++++++++++++++++++++++Functions++++++++++++++++++++++++++++++++++++++++++++++++++++++++++++++++++++++++++++++++
//++++++++++++++++++++++++++++++++++++++++++++++++++++++++++++++++++++++++++++++++++++++++++++++++++++++++++++++++++++++++++++++++++++++++++++++++++++++



//*******************************************************************************************************
//******************************************Interrupts****************************************************
//********************************************************************************************************
void interruptOpen()
{
  interruptFlagO++;
#ifdef DEBUG
  Serial.println("An interrupt (open) has occurred!");
  Serial.println("Counter:");
  Serial.println(interruptFlagO);
#endif
}

void interruptClose()
{
  interruptFlagC++;
#ifdef DEBUG
  Serial.println("An interrupt (close) has occurred!");
  Serial.println("Counter:");
  Serial.println(interruptFlagC);
#endif
}



//*******************************************************************************************************
//******************************************Calibration Door****************************************************
//********************************************************************************************************

void calibration()
{
  Serial.println("Calibration in progress");
  //delay(5000);
  digitalWrite(enPin, LOW); //Enable Driving Stage

  interruptFlagO = 0;

  door1.setMaxSpeed(calVelocity);
  door1.setAcceleration(acceleration);

  //firstly, drive to right (open) ONLY if the endstop is not activated (door open alread)
  if (digitalRead(interruptOpenPin) != LOW)
  {
    while (true)
    {
      door1.setSpeed(calVelocity);
      door1.runSpeed();
      if (interruptFlagO > 0)
      {
        break;
      }
    }
  }

  door1.setCurrentPosition(0);
  delay(1000);

  interruptFlagC = 0;
  //while(interruptFlagC == 0)

  while (true)
  {
    door1.setSpeed(-calVelocity);
    door1.runSpeed();
    if (interruptFlagC > 0)
    {
      break;
    }
  }
  maxSteps = abs(door1.currentPosition());
  door1.setCurrentPosition(0);
  delay(2000);
  //digitalWrite(enPin, HIGH); //Disable Driving Stage

  Serial.println("Calibration done!");
}


//*******************************************************************************************************
//******************************************Close Door****************************************************
//********************************************************************************************************
void closeDoorFunc() {
  //Only close door if endstop not activated
  if (!digitalRead(interruptClosePin)) {
    #ifdef DEBUG
    Serial.println("Door closes!");
    #endif

    digitalWrite(enPin, LOW); //Enable Driving Stage
    interruptFlagC = 0; //Reset InterruptCounter
    door1.setMaxSpeed(0); //Set all velocity variable in the library to zero (BUG)

    //Check current position if door is in main speed section
    if (curPos > minVelSteps) {
      MoveDoor();
      //if during main speed phase closing, mqtt message 'open door' was received, start breaking in closing direction
      if (closeDoor == false) {
        Brake("brakeClose");
        return; //after braking leave openDoorFunc
      }
    } //Door reached minVelSteps or stopped due to new input in mqtt_loop


    //check current position if door is in slow speed section
    if (curPos <= minVelSteps) {
      MoveDoorSlow();
    }
    #ifdef DEBUG
    Serial.println("Door closed!");
    #endif
  }
}
//*******************************************************************************************************
//******************************************Open Door****************************************************
//********************************************************************************************************
void openDoorFunc() {

  //Only open door if endstop not activated (different level than close endstop!)
  if (digitalRead(interruptOpenPin)) {
    #ifdef DEBUG
    Serial.println("Door opens!");
    #endif
    digitalWrite(enPin, LOW); //Enable Driving Stage
    interruptFlagO = 0; //Reset InterruptCounter
    door1.setMaxSpeed(0); //Set all velocity variable in the library to zero (BUG)

    //Check current position if door is in main speed section
    if (curPos < (maxSteps - minVelSteps)) {
      MoveDoor();
      //if during main speed section closing, mqtt message 'close door' was received, start breaking in opening direction
      if (openDoor == false) {
        Brake("brakeOpen");
        return; //after braking leave openDoorFunc
      }
    }//Door reached minVelSteps or stopped due to new input in mqtt_loop

    //check current position if door is in slow speed section
    if (curPos >= (maxSteps - minVelSteps)) {
      MoveDoorSlow();
    }
    #ifdef DEBUG
    Serial.println("Door open!");
    #endif
  }
}

//*******************************************************************************************************
//****************************************** Brake ****************************************************
//********************************************************************************************************

void Brake(String brakeDirection) {
  //Moving Parameters
  door1.setMaxSpeed(maxVelocity);
  door1.setAcceleration(accelerationBreak);

  if (brakeDirection == "brakeOpen") {
    endPosition = curPos + breakStepsInput;
    //avoid additional acceleration if calculated endposition is greater then max value
    if (endPosition > maxSteps) {
      endPosition = maxSteps;
    }

    door1.moveTo(endPosition);
    while (curPos < endPosition) {
      door1.run();
      curPos = door1.currentPosition();

      //Enstop touched. Safety, if calibration parameters are incorrect
      if (interruptFlagO > 0) {
        delay(1000); //to prevent door from moving freely with rest impuls
        digitalWrite(enPin, HIGH); //Disable Driving Stage
        break;
      }
    }
  }

  else if (brakeDirection == "brakeClose") {
    endPosition = curPos - breakStepsInput;
    //avoid additional acceleration if calculated endposition is greater then max value
    if (endPosition < 0) {
      endPosition = 0;
    }
    door1.moveTo(endPosition);
    while (curPos > endPosition) {
      door1.run();
      curPos = door1.currentPosition();

      //Enstop touched. Safety, if calibration parameters are incorrect
      if (interruptFlagC > 0) {
        //delay(1000); //to prevent door from moving freely with rest impuls
        //digitalWrite(enPin, HIGH); //Disable Driving Stage
        break;
      }
    }
  }
}

//*******************************************************************************************************
//****************************************** MoveDoor ****************************************************
//********************************************************************************************************

void MoveDoor() {

  //Moving Parameters
  door1.setMaxSpeed(maxVelocity);
  door1.setAcceleration(acceleration);

  if (openDoor == true) {
    door1.moveTo(maxSteps - minVelSteps + breakSteps);
    //Open Door up to position where continuing with constant speed
    while ((curPos < (maxSteps - minVelSteps)) && openDoor == true) {
      door1.run();
      curPos = door1.currentPosition();
      mqtt_loop();

      //Enstop touched. Safety, if calibration parameters are incorrect
      if (interruptFlagO > 0) {
        delay(1000); //to prevent door from moving freely with rest impuls
        digitalWrite(enPin, HIGH); //Disable Driving Stage
        return;
      }
    }
  }

  else if (closeDoor == true) {
    door1.moveTo(minVelSteps - breakSteps);
    //Close Door up to position where continuing with constant speed
    while (curPos > minVelSteps && closeDoor == true) {
      door1.run();
      curPos = door1.currentPosition();
      mqtt_loop();

      //Enstop touched. Safety, if calibration parameters are incorrect
      if (interruptFlagC > 0)
      {
      delay(1000);
      digitalWrite(enPin, HIGH); //Disable Driving Stage
      #ifdef DOOR1
      //send closed door message to disable plasma globe puzzle
      mqtt_publish("4/door/entrance", "message", "door_1_closed");
      //avoid reopening if plasma globes are released before they read the message
      delay(1000);
      mqtt_loop();
      if(openDoor == true) openDoor = false;
      #endif
      return;
      }
    }
  }
}

//*******************************************************************************************************
//****************************************** MoveDoorSlow ****************************************************
//********************************************************************************************************

void MoveDoorSlow() {
  //Moving Parameters
  door1.setMaxSpeed(minVelocity);
  door1.setAcceleration(acceleration);

  if (openDoor == true) {
    door1.moveTo(maxSteps + moveOn);
    while ((curPos < (maxSteps + moveOn)) && (openDoor == true)) {
      door1.run();
      curPos = door1.currentPosition();
      mqtt_loop();

      if (interruptFlagO > 0) {
        delay(1000);
        digitalWrite(enPin, HIGH); //Disable Driving Stage
        return;
      }
    }
  }

  else if (closeDoor == true) {
    door1.moveTo(-moveOn);
    while ((curPos > (-moveOn)) && closeDoor == true) {
      door1.run();
      curPos = door1.currentPosition();
      mqtt_loop();

      if (interruptFlagC > 0) {
        delay(1000);
        digitalWrite(enPin, HIGH); //Disable Driving Stage
        #ifdef DOOR1
        //send closed door message to disable plasma globe puzzle
        mqtt_publish("4/globes", "message", "door_1_closed");
        //avoid reopening if plasma globes are released before they read the message
        delay(1000);
        mqtt_loop();
        if(openDoor == true) openDoor = false;
        #endif
        return;
      }
    }
    if(closeDoor == true){
      //this section of the code is only reached if door moves below zero (happens if endstop is damaged)
      delay(1000);
      digitalWrite(enPin, HIGH); //Disable Driving Stage
      #ifdef DEBUG1
      //send closed door message to disable plasma globe puzzle
      mqtt_publish("4/door/entrance", "message", "door_1_closed");
      //avoid reopening if plasma globes are released before they read the message
      delay(1000);
      mqtt_loop();
      if(openDoor == true) openDoor = false;
      #endif
    }
  }
}

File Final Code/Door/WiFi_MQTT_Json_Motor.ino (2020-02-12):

/*
 Doors

 This code 
 - establishes Wifi connection
 - establishes MQTT protocoll
 - handles JSON communication to server/ other uC
 - enables Over The Air updates (OTA)
*/
#include "WiFi_MQTT_Json_Motor.h"

#define DEBUG

//EEPROM addressing
#define MAX_MDNS_LEN 16
#define MDNS_START_ADDRESS 0
#define MAX_WIFI_LEN 32
#define WIFI_SSID_START_ADDRESS 32
#define WIFI_PWD_START_ADDRESS 64

//Wifi credentials 
char ssid[] = "ubilab_wifi";
char password[] = ;

//MQTT variables
//IP address of computer which runs mqtt server (broker) --> mqtt main server ip: 10,0,0,2
const IPAddress mqttServerIP(10,0,0,2);
//mqtt device id
#ifdef DOOR1
char clientId[] = "Group4_Door_Entrance";
#endif
#ifdef DOOR2
char clientId[] = "Group4_Door_Server";
#endif

//--------------------------------------------------------------------------------------------------------------------------------------------------------
/*
 * function setup_wifi
 * param: none
 * return: none
 * purpose: configure WiFi and connect to network
 */
void setup_wifi() {
  
  WiFi.disconnect(true);
  delay(1000);
  WiFi.mode(WIFI_STA);
  delay(1000);
  
  //2x WiFi.begin necessary for connection
  WiFi.begin(ssid, password);
  delay(1000);
  WiFi.begin(ssid, password);

  //try connecting 
  long timer = millis();
  while (millis() - timer < 10000) {
    if (WiFi.status() == WL_CONNECTED) break;
    delay(5000);
    #ifdef DEBUG
    Serial.print(".");
    #endif 
    WiFi.begin(ssid, password);
  }
  
  //restart ESP if connection failed
  if (WiFi.status() != WL_CONNECTED) {
    #ifdef DEBUG
    Serial.println("Connection Failed! Rebooting...");
    #endif 
    delay(100);
    ESP.restart();
  }

}

//--------------------------------------------------------------------------------------------------------------------------------------------------------
/*
 * function setupOTA
 * param: none
 * return: none
 * purpose: establish OTA 
 */
void setupOTA() {
  
  // Hostname defaults to esp3232-[MAC]
  #ifdef DOOR1
  ArduinoOTA.setHostname("Door1");
  #endif
  #ifdef  DOOR2
  ArduinoOTA.setHostname("Door2");
  #endif

  ArduinoOTA.setPassword("group4");

  ArduinoOTA.onStart([]()
  {
    String type;
    if (ArduinoOTA.getCommand() == U_FLASH)
      type = "sketch";
    else // U_SPIFFS
      type = "filesystem";

    // NOTE: if updating SPIFFS this would be the place to unmount SPIFFS using SPIFFS.end()
    #ifdef DEBUG
    Serial.println("Start updating " + type);    
    #endif 
  })
  .onEnd([]()
  {
    #ifdef DEBUG
    Serial.println("\nEnd");    
    #endif 
  })
  .onProgress([](unsigned int progress, unsigned int total) {
    #ifdef DEBUG
    Serial.printf("Progress: %u%%\r", (progress / (total / 100)));    
    #endif 
  })
  .onError([](ota_error_t error)
  {
    #ifdef DEBUG
    Serial.printf("Error[%u]: ", error);    
    #endif 
    if (error == OTA_AUTH_ERROR) Serial.println("Auth Failed");
    else if (error == OTA_BEGIN_ERROR) Serial.println("Begin Failed");
    else if (error == OTA_CONNECT_ERROR) Serial.println("Connect Failed");
    else if (error == OTA_RECEIVE_ERROR) Serial.println("Receive Failed");
    else if (error == OTA_END_ERROR) Serial.println("End Failed");
  });

  ArduinoOTA.begin();
    #ifdef DEBUG
    Serial.println("Ready");
    Serial.print("IP address: ");
    Serial.println(WiFi.localIP());    
    #endif 
}


//--------------------------------------------------------------------------------------------------------------------------------------------------------
/*
 * function setup_mqtt
 * param: none
 * return: none
 * purpose: define mqtt broker (server) and set callback fct to receive messages published to subscribed topics
 */
void setup_mqtt(){
  
  client.setServer(mqttServerIP, 1883);
  client.setCallback(mqtt_callback);
}


//--------------------------------------------------------------------------------------------------------------------------------------------------------
/*
 * function mqtt_callback
 * param: -topic: name of the topic wich has a new message
 *        -payload: the message itself
 *        -length: length of the message
 * return: none
 * purpose: Callback function is fired each time a message is published in any of the subsribed topics
 */
void mqtt_callback(char* topic, byte* payload, unsigned int length) {
  /*
  #ifdef DEBUG
  Serial.print("Message arrived [");
  Serial.print(topic);
  Serial.print("] ");
  for (int i = 0; i < length; i++) {
    Serial.print((char)payload[i]);
  }
  Serial.println();
  #endif
  */
  
  //Deserialize
  StaticJsonDocument<300> doc;
  // Deserialize the JSON document
  DeserializationError error = deserializeJson(doc, payload);

  // Test if parsing succeeds.
  if (error) {
    Serial.print(F("deserializeJson() failed: "));
    Serial.println(error.c_str());
    return;
  }

  String Method = doc["method"];
  String State = doc["state"];
  String Data = doc["data"]; //should be 0 if no data argument was received (see https://arduinojson.org/v6/doc/deserialization/ --> 3.3.3 in pdf)
  
  //Act according to trigger value
  /*********************** trigger: on ****************************/
  if(Method == "trigger" && State == "on"){

    //set opening flag
    openDoor = true;
    closeDoor = false;

    //respond to activation message
    //{"method":"STATUS","state":"active", "data":"opening"}
    //mqtt_publish("4/door/entrance", "status", "active", "opening");

  }
  /*********************** trigger: off ****************************/
  if(Method == "trigger" && State == "off"){

    //set closing flag
    closeDoor = true;
    openDoor = false;

    //respond to activation message
    //{"method":"STATUS","state":"active", "data":"closing"}
    //mqtt_publish("4/door/entrance", "status", "active", "closing");

  }  

  /*********************** restart esp ****************************/  
  else if (Method == "message" && State == "restart"){
    ESP.restart();

  }

}
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

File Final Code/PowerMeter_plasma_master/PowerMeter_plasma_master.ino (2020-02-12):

#include <SPI.h>
#include "STPM.h"
#include <ESP8266WiFi.h>
// #include <esp_wifi.h>
#include <WiFiClient.h>
#include <WiFiUdp.h>
#include <PubSubClient.h>
#include <ArduinoJson.h>
#include "WiFi_MQTT_Json_Plasma_Master.h"

#include <EEPROM.h>

#include <ESP8266mDNS.h>

// Arduino Updater
#include <ArduinoOTA.h>

// Serial Speed and DEBUG option
// #define SERIAL_SPEED 2000000
#define SERIAL_SPEED 115200
#define DEBUG


#define MAX_MDNS_LEN 16
#define MDNS_START_ADDRESS 0
// Pins for STPM34 SPI Connection
const int STPM_CS = 15;
const int STPM_SYN = 4;
// Reset pin of STPM
const int STPM_RES = 5;

// Pins for 230V Relay
const int RELAY_PIN = 2;

// STPM Object
STPM stpm34(STPM_RES, STPM_CS, STPM_SYN);


// WLAN configuration
const char *ssids[] = {"ubilab_wifi"};
const char *passwords[] = ; //use {"pwd"}

char mdnsName[MAX_MDNS_LEN] = {'\0'};

WiFiUDP udp;

long mdnsUpdate = millis();

//door status: open = 1, close = 0
bool door_status = 1;

//Globe ID
int globeID = 1;
//touch status flags
bool current_touch = 0;
bool old_touch = 0;

//touch recognition
const int numReadings = 25;

//variables for moving average over current samples
float readings[numReadings] = {0};      // current readings
int readIndex = 0;              // the index of the current reading
float total = 0;                  // the running total
float averageInputValue = 0;

float RMScurrent = 0;
float RMSvoltage = 0;

//base reading at the beginning of
int baseline_count = 100; // the number of readings at the beginning whose average sets the baseline 
float baseline = 0;

//factor for recognizing touch
float touch_factor = 0.15;

/************************ SETUP *************************/
void setup() {
  // Set Relay pins as output which should be switched on by default
  pinMode(RELAY_PIN, OUTPUT);
  //turn the plasma globe on initially for baseline reading
  digitalWrite(RELAY_PIN, HIGH);

   // Setup serial communication
  Serial.begin(SERIAL_SPEED);


  // Setup STPM 32
  stpm34.init();

  // Load the MDNS name from eeprom
  EEPROM.begin(2*MAX_MDNS_LEN);

  #ifdef DEBUG
  Serial.println("Info:Connecting WLAN ");
  #endif
  WiFi.mode(WIFI_STA);
  // esp_wifi_set_ps(WIFI_PS_NONE);
  wifi_set_sleep_type(NONE_SLEEP_T);
  char * name = getMDNS();
  WiFi.hostname(name);
  connectNetwork();

  initMDNS();
  setup_mqtt();

  WiFi.setOutputPower(20.5);

  setupOTA();

  mdnsUpdate = millis();
  
  //extract Globe ID from mdns name
  char * eeprom_name = getMDNS();
  String id = "1";
  if (strlen(eeprom_name) == 0) {
    #ifdef DEBUG
    Serial.print(F("No MDNS Name in EEPROM, Globe ID fixed to 1"));
    #endif
  }
  else{
    //globeID = (int) eeprom_name[5]
    //remember char to int (ASCII)
    globeID = eeprom_name[5] - 48;
  }
  //get baseline
  //first current after power on is way higher than baseline --> delay
  delay(2000);
  for(int i = 0; i < baseline_count; i++){
    
      stpm34.readRMSVoltageAndCurrent(1, &RMSvoltage, &RMScurrent);
      baseline += RMScurrent;
      delay(10);
  }
  baseline /= baseline_count;
  //re-initialize the moving average array with the baseline readings
  for(int i = 0; i<numReadings; i++){
    readings[i] = baseline;
    total += baseline;
  }
  
  #ifdef DEBUG
  Serial.print(F("baseline = "));
  Serial.println(baseline);
  #endif

  //turn plasma globe off after baseline reading
  digitalWrite(RELAY_PIN, LOW);

}

// the loop routine runs over and over again forever:
void loop() {
  
  if (WiFi.status() != WL_CONNECTED) {
    connectNetwork();
    mdnsUpdate = millis();
  }

  // Arduino OTA
  ArduinoOTA.handle();

  // Update mdns
  MDNS.update();
  // Re-advertise service
  if ((long)(millis() - mdnsUpdate) >= 0) {
    MDNS.addService("elec", "tcp", 54322);
    mdnsUpdate += 100000;
  }


  mqtt_loop();
  
  if(globe_status == true){
    
    //application: touch recognition
    //subtract the last reading:
    total = total - readings[readIndex];
  
    // read from the sensor:
    stpm34.readRMSVoltageAndCurrent(1, &RMSvoltage, &RMScurrent);
    readings[readIndex] = RMScurrent;
    delay(10);
  
    // add the reading to the total:
    total = total + readings[readIndex];
    // advance to the next position in the array:
    readIndex = readIndex + 1;

    // if we're at the end of the array...
    if (readIndex >= numReadings) {
    // ...wrap around to the beginning:
    readIndex = 0;
    }

    // Calculate the average input value.
    averageInputValue = total / numReadings;
    //if globe is touched
    if(averageInputValue > (1+touch_factor)*baseline){

      #ifdef DEBUG
      Serial.println("TOUCHED");
      #endif 

      current_touch = 1;
      //only send touched message if this globe was NOT touched before
      if(current_touch == 1 && old_touch == 0){
        
         mqtt_publish("4/globes", "message", "touched", String(globeID));
         globe_0 = 1;
      }
      
      old_touch = 1;
      
    }
    else{

      current_touch = 0;
      //only send NOT_touched message if this globe was touched before
      if(current_touch == 0 && old_touch == 1){
        
         mqtt_publish("4/globes", "message", "NOT_touched", String(globeID));
         globe_0 = 0;
      }
      
      old_touch = 0;
      //Serial.println("NOT TOUCHED");
    }

    //check if all globes are touched and door is open currently /in opening process
    if(((globe_0 + globe_1 + globe_2 + globe_3) == participants) && door_status == 1){

      //all globes are touched! --> close the door
      mqtt_publish("4/door/entrance", "trigger", "off");
      door_status = 0;
    }
    //if not all globes are touched and door is closed currently/ in closing process
    else if(((globe_0 + globe_1 + globe_2 + globe_3) < participants) && door_status == 0){

      //NOT all globes are touched! --> close the door
      mqtt_publish("4/door/entrance", "trigger", "on");
      door_status = 1;
    }
  
  }
  
  yield();
}

void setupOTA() {

  // No authentication by default
  ArduinoOTA.setPassword("group4");

  ArduinoOTA.onStart([]() {
    Serial.println("Start updating");
    // free(buffer);
  });

  ArduinoOTA.onEnd([]() {
    Serial.println("\nEnd");
  });
  ArduinoOTA.onProgress([](unsigned int progress, unsigned int total) {
    Serial.printf("Progress: %u%%\r", (progress / (total / 100)));
  });
  ArduinoOTA.onError([](ota_error_t error) {
    Serial.printf("Error[%u]: ", error);
    if (error == OTA_AUTH_ERROR) {
      Serial.println("Auth Failed");
    } else if (error == OTA_BEGIN_ERROR) {
      Serial.println("Begin Failed");
    } else if (error == OTA_CONNECT_ERROR) {
      Serial.println("Connect Failed");
    } else if (error == OTA_RECEIVE_ERROR) {
      Serial.println("Receive Failed");
    } else if (error == OTA_END_ERROR) {
      Serial.println("End Failed");
    }
    // No matter what happended, simply restart
    WiFi.forceSleepBegin();
    wdt_reset();
    ESP.restart();
    while(1) wdt_reset();
  });

  ArduinoOTA.begin();
}
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

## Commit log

2019-11-06 inserted Marios part (puzzle idea) into this file
2019-11-13 Create MotorControl
2019-11-14 added BOM
    [BOM.xlsx]
2019-11-15 added DC/DC converters and changed power source to 24V
    [BOM.xlsx]
2019-11-25 Completely new MotorControl Code
    includes:
    -Calibration function
    -Serial Command Function
    -Open Door Function
    -Close Door Function
2019-12-06 first plasma globe test-->output voltage esp32 adc
2019-12-20 Update MotorControl
2019-12-20 edit readme, upload plasma globe measurement with PowerMeter
2020-01-08 Current Riddle Arduino File
2020-01-11 deleted MotorControl
2020-01-14 Create MotorControl_BasicOTA.ino
    Control Software for the stepper motor of the entrance door. MQTT and OTA (Mario's Version) are included.
2020-01-27 added folder for final code with current door1 code
2020-02-06 added gyrophare control within door code
2020-02-07 adapted door code to prevent opening after plasma globes are turned off
    [Door.ino]
2020-02-09 corrected error in flow chart
2020-02-12 changed writing method of lcd, codes do not compile until wifi cred. are enteres --> prevents OTA upload without credentials, publish messages updated
    [First_Puzzle_final.ino, PowerMeter_plasma_master.ino, PowerMeter_plasma_slaves.ino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]
2020-02-12 Update README.md
    added 3d printed things
